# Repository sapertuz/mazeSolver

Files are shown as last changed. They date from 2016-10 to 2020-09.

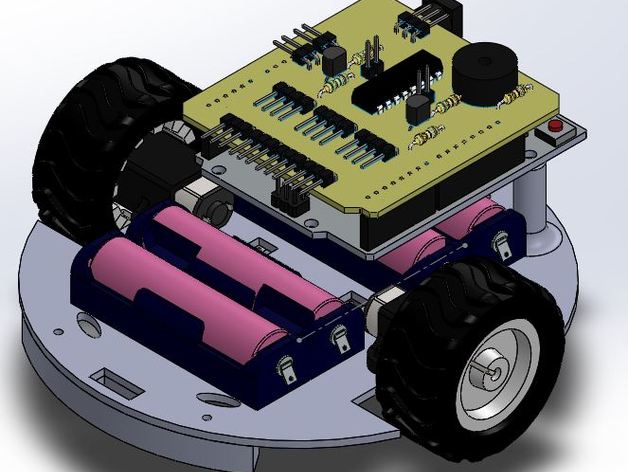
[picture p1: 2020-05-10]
Maze_Solver/images/dd3d5e054d19bdba38d1fe2deb0f85b0_preview_featured.JPG

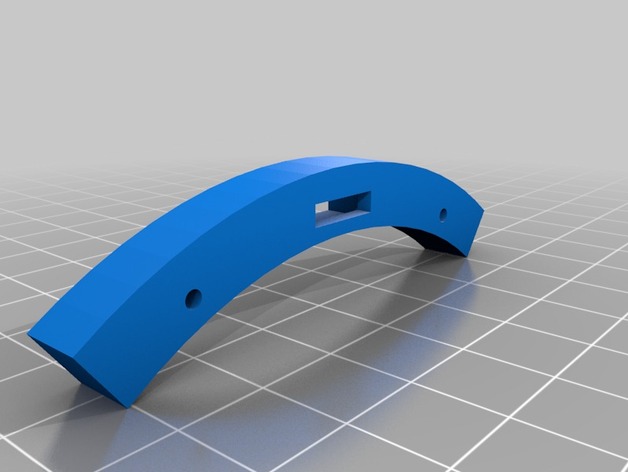
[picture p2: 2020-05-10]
Maze_Solver/images/59abfc2566f2f89f3f8ee435759e22d9_preview_featured.jpg

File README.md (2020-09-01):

<h1 align="center">Open-Source mazeSolver</h1>
<div align="center">

<i>A Maze Solving Line Follower Using Arduino</i>








Awesome Badge

<!-- <img src="http://hits.dwyl.com/cheiio/mazeSolver.svg" alt="Hits Badge"/> -->

<br>
<i>Loved the project? Please consider giving a Star ⭐️ to help it improve!</i>

</div>

# mazeSolver

<a href="https://github.com/cheiio/mazeSolver">
  Twitter
</a>

This Git contains the 
- Arduino Project Source  https://github.com/cheiio/mazeSolver/tree/master/Arduino_src
- Eagle Source for PCB board  https://github.com/cheiio/mazeSolver/tree/master/Laberinto
- SolidWorks files of parts to be printed  https://github.com/cheiio/mazeSolver/tree/master/Maze_Solver/files

This is the arduino program running ont he maze solver project viewed in http://www.thingiverse.com/thing:1690543
You need the PID_v1 library fot arduino to make irt run

This is a current working project. It's a 3D printed Maze Solver and Line Follower based on the Pololu 3Pi robot.
It uses a Arduino Leonardo and a custom made shield.
<br />

## Materials

***<details><summary>Click Me For Materials!GIF</summary>***
  
* Arduino Leonardo
* L293D
* Piezo Buzzer
* QTR-1RC Reflectance Sensor (2-Pack) x 2 (https://www.pololu.com/product/2459)
* QTR-8A Reflectance Sensor Array (Only the cutted 2 sensor at the left) https://www.pololu.com/product/960
* 75:1 Micro Metal Gearmotor HPCB 6V (https://www.pololu.com/product/3064)
* Pololu Wheel 42×19mm Pair (https://www.pololu.com/product/1090)
* Pololu Micro Metal Gearmotor Bracket Pair
* (https://www.pololu.com/product/989)
* Pololu Ball Caster with 1/2″ Metal Ball (https://www.pololu.com/product/953)
* 2-AA Batteries
* 2-AA Battery Holder (https://www.pololu.com/product/1150)
</details>
<br />

### Robot In Action

<a href="https://www.youtube.com/watch?v=Ddkci5myxYI" target="_blank">
GIF
</a>
<br />

## CAD Files

</a>
<a href="https://github.com/cheiio/mazeSolver/tree/master/Maze_Solver/files/" >
  CAD Files
</a>
</a>
<a href="https://github.com/cheiio/mazeSolver/tree/master/Maze_Solver/files/" >
  CAD Files
</a>
</a>
<a href="https://github.com/cheiio/mazeSolver/tree/master/Maze_Solver/files/" >
  CAD Files
</a>

<br /><br />

## Line Follower Photos

CAD Files
CAD Files

<br />

## YouTube Video
</a>
<a href="https://www.youtube.com/watch?v=Ddkci5myxYI&feature=youtu.be" >
  CAD Files
</a>

For Robot in action Please checkout my<br />
**Youtube Channel  [Click Here](https://www.youtube.com/watch?v=Ddkci5myxYI&feature=youtu.be)** .<br /><br /><br />

If You Found this Project Useful in any manner <br />
**Subscribe** my **Youtube Channel  [Click Here](https://www.youtube.com/user/Sapmcool)** .<br />

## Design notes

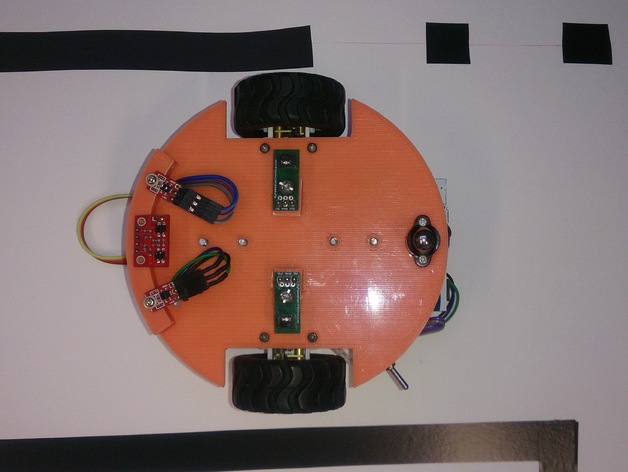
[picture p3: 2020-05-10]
Maze_Solver/images/c2a115ca9fa706efb5667b804ab19a76_preview_featured.JPG

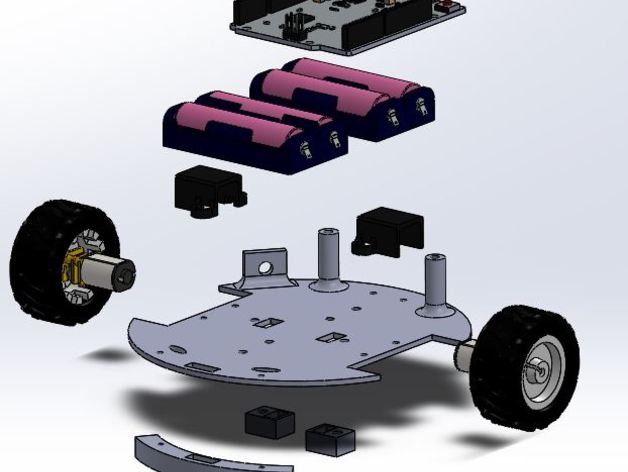
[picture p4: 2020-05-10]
Maze_Solver/images/6491ceb7f1e24ea76eec02fb2ce37934_preview_featured.JPG

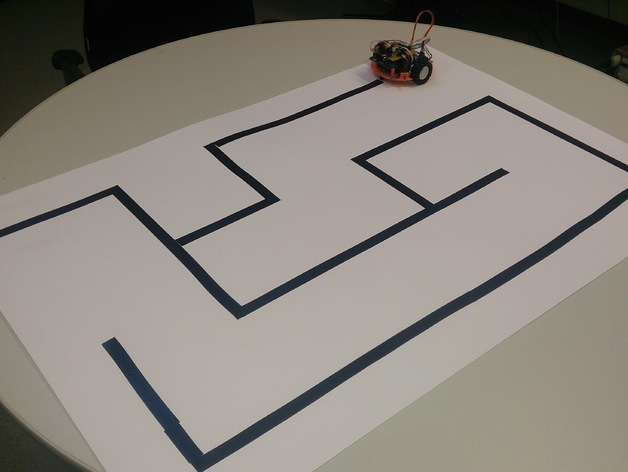
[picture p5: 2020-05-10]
Maze_Solver/images/3bacaf6ce22a14ae35e1a1dbc1d07312_preview_featured.JPG

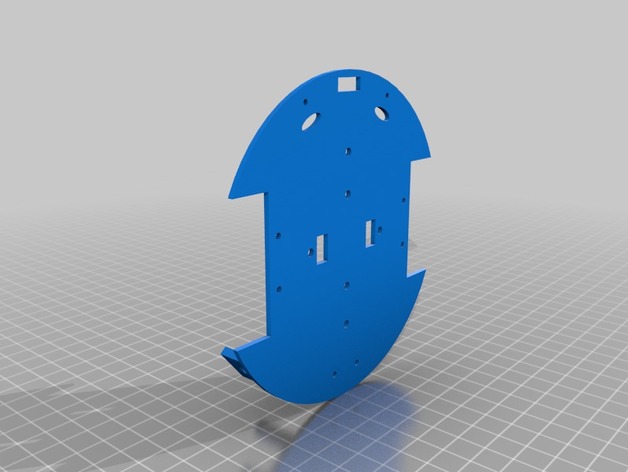
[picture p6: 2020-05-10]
Maze_Solver/images/ea35e3248423d630fb57c955e7d1f504_preview_featured.jpg

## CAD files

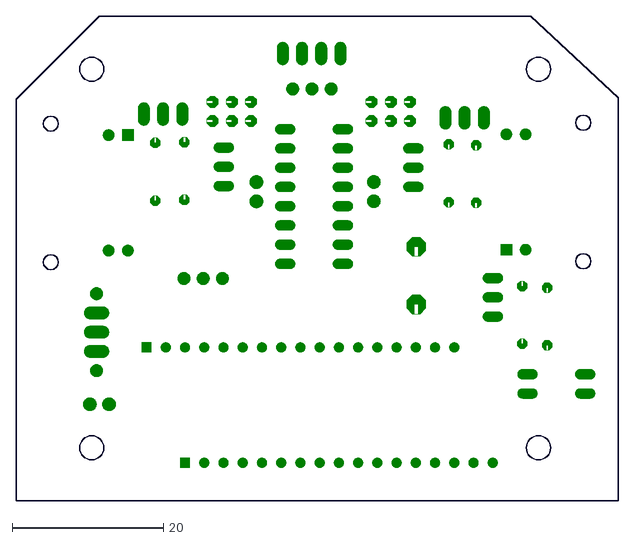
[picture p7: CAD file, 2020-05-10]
Laberinto/placa.dxf
79.5 x 64.0

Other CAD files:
Maze_Solver/files/2.STEP
Maze_Solver/files/1.STEP
Maze_Solver/files/base.STEP
Maze_Solver/files/1.SLDPRT
Maze_Solver/files/1.STL
Maze_Solver/files/2.SLDPRT
Maze_Solver/files/2.STL
Maze_Solver/files/base.SLDPRT
Maze_Solver/files/base.STL

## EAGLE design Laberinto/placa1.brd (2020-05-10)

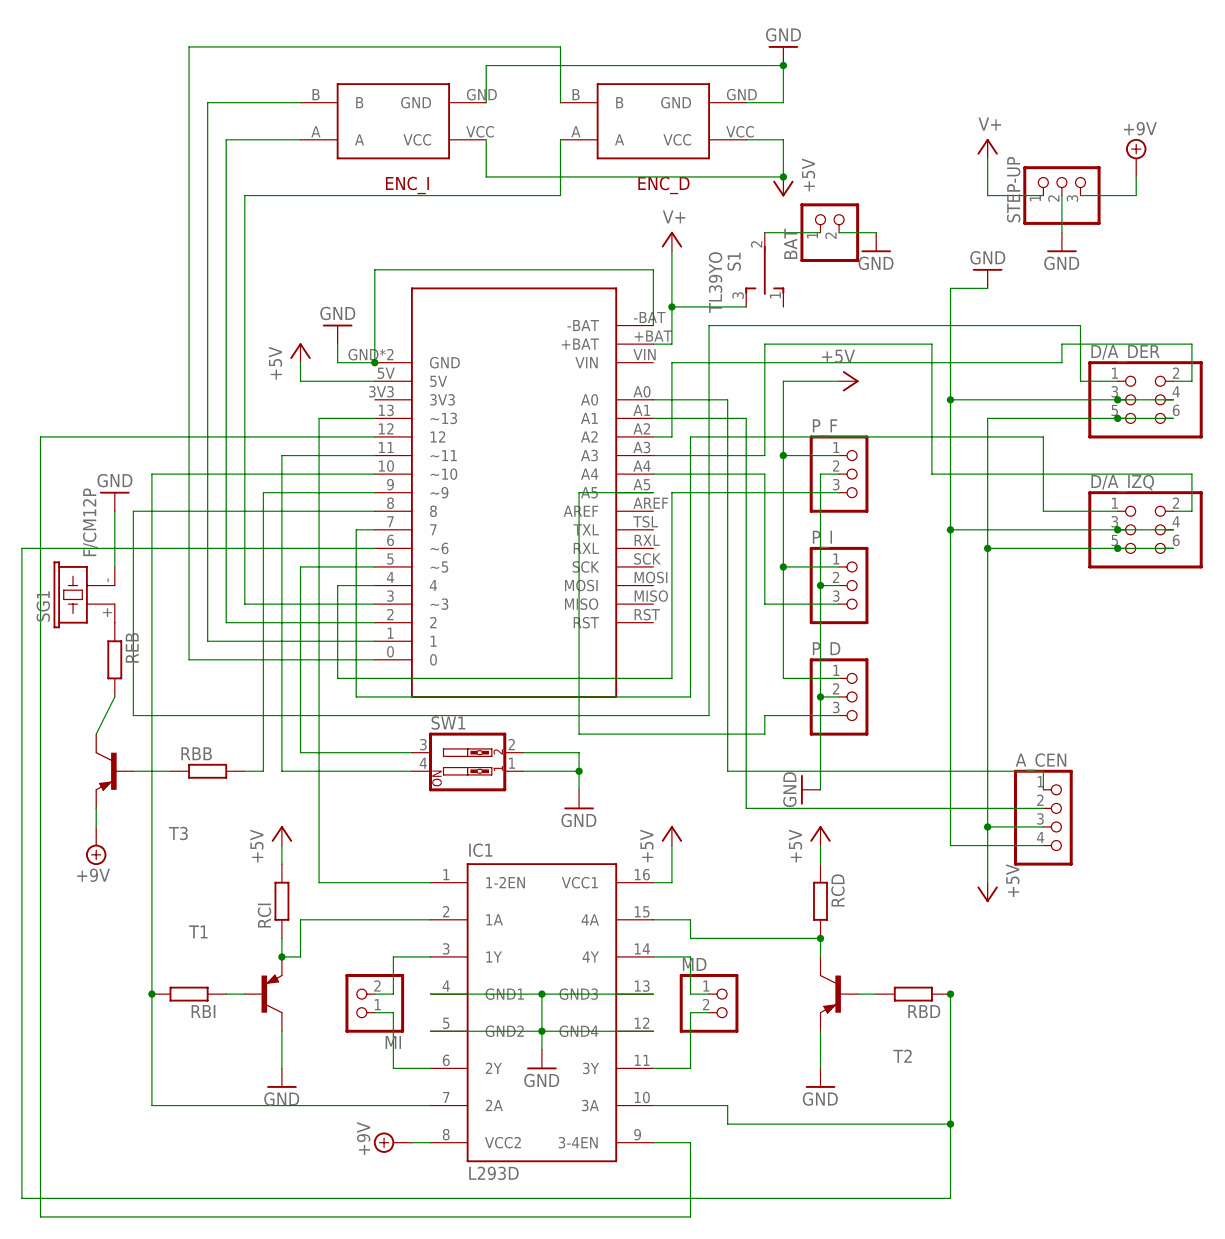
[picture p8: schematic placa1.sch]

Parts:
A_CEN: PINHD-1X4/90; 1X04/90
BAT: PINHD-1X2; 1X02
D/A_DER: PINHD-2X3/90; 2X03/90
D/A_IZQ: PINHD-2X3/90; 2X03/90
ENC_D: POLOLU_ENCODER
ENC_I: POLOLU_ENCODER
IC1: L293D; DIL16
MD: PINHD-1X2; 1X02
MI: PINHD-1X2; 1X02
P_D: PINHD-1X3/90; 1X03/90
P_F: PINHD-1X3; 1X03
P_I: PINHD-1X3/90; 1X03/90
RBB: R0204/7; 0204/7
RBD: R0204/7; 0204/7
RBI: R0204/7; 0204/7
RCD: R0204/7; 0204/7
RCI: R0204/7; 0204/7
REB: R0204/7; 0204/7
S1: TL39YO; TL3XYO
SG1: F/CM12P
STEP-UP: PINHD-1X3; 1X03
SW1: SW_DIP-2; EDG-02
T1, T2, T3: -PNP-TO92-BEC; TO92-BEC
U$1: A-STAR_LV

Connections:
+5V: A_CEN.3, D/A_DER.5, D/A_DER.6, D/A_IZQ.5, D/A_IZQ.6, ENC_D.VCC, ENC_I.VCC, IC1.16 (VCC1), P_D.1, P_F.1, P_I.1, RCD.1, RCI.2, U$1.5V
+9V: IC1.8 (VCC2), STEP-UP.3, T3.E
GND: A_CEN.4, BAT.2, D/A_DER.3, D/A_DER.4, D/A_IZQ.3, D/A_IZQ.4, ENC_D.GND, ENC_I.GND, IC1.4 (GND1), IC1.5 (GND2), IC1.12 (GND4), IC1.13 (GND3), P_D.2, P_F.2, P_I.2, SG1.- (2), STEP-UP.2, SW1.1, SW1.2, T1.C, T2.E, U$1.-BAT, U$1.GND, U$1.GND2 (GND)
unnamed: BAT.1, S1.2
unnamed: IC1.2 (1A), RCI.1, T1.E
unnamed: RBI.1, T1.B
unnamed: RBD.2, T2.B
unnamed: IC1.15 (4A), RCD.2, T2.C
unnamed: IC1.11 (3Y), MD.2
unnamed: IC1.14 (4Y), MD.1
unnamed: IC1.7 (2A), RBI.2, U$1.10 (~10)
unnamed: IC1.3 (1Y), MI.2
unnamed: IC1.6 (2Y), MI.1
unnamed: IC1.10 (3A), RBD.1, U$1.6 (~6)
unnamed: REB.2, T3.C
unnamed: REB.1, SG1.+ (1)
unnamed: RBB.1, T3.B
unnamed: ENC_I.A, U$1.2
unnamed: ENC_D.B, U$1.0
unnamed: ENC_I.B, U$1.1
unnamed: IC1.9 (3-4EN), U$1.12
unnamed: SW1.3, U$1.5 (~5)
unnamed: SW1.4, U$1.11 (~11)
unnamed: RBB.2, U$1.9 (~9)
unnamed: ENC_D.A, U$1.3 (~3)
unnamed: IC1.1 (1-2EN), U$1.13 (~13)
unnamed: P_F.3, U$1.4
unnamed: D/A_IZQ.1, U$1.7
unnamed: D/A_DER.1, U$1.8
unnamed: A_CEN.1, U$1.A0
unnamed: D/A_IZQ.2, U$1.A3
unnamed: P_I.3, U$1.A4
unnamed: P_D.3, U$1.A5
unnamed: A_CEN.2, U$1.A1
unnamed: D/A_DER.2, U$1.A2
V+: S1.3 (S), STEP-UP.1, U$1.+BAT

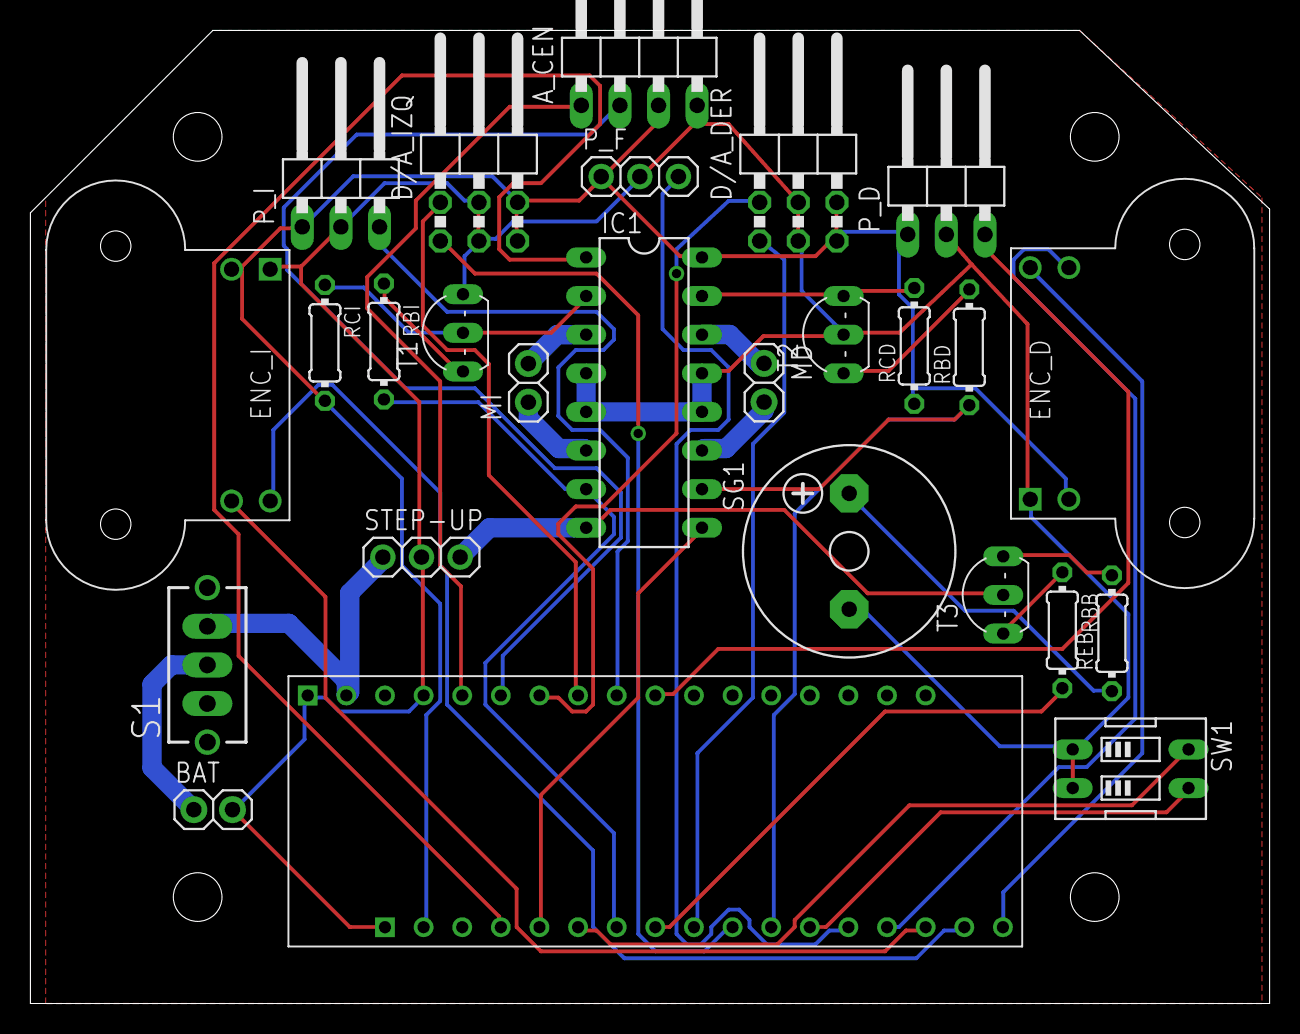
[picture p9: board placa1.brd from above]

Board: 2 copper layers, 81.5 x 64.0 mm, 26 parts (0 on the bottom side), 36 nets.

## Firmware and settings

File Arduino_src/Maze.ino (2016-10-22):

#include <PID_v1.h>

#define s3 A0
#define s1 A3
#define s2 A2
#define s0 A1
#define QRDR 7
#define QRDL 4
#define BUZZ 11
#define ENAL 5
#define ENAR 6
#define GIRL 13
#define GIRR 12

#define C  523
#define CS  524
#define D  587
#define DS  622
#define E  659
#define FA  698
#define FS  740
#define G  784
#define GS  830
#define A  880
#define AS  932
#define B  988

const unsigned int ini_notes[] = {660,660,660,510,660,770,380};
const unsigned int ini_beat[] = {100,100,100,100,100,100,100};
const unsigned int ini_mute[] ={150,300,300,100,300,550,575};

const unsigned int fin_notes[] = {G,C,E,G,C,E,C,G, GS,CS,FA,GS,CS,GS, AS,DS,G,AS,DS,G,DS, DS,DS,DS, C};
const unsigned int fin_beat[] = {100,100,100,100,100,100,100,150,100, 100,100,100,100,100,100,100,150,100, 100,100,100,100,100,100,100,150, 40,40,40, 150};

const int maxpwm = 255; // the maximum speed
const int cal=200;

int path[100], path_step = 0;

int i, x, k, ts = 50, spin = 40, halftape=100, lilbit=20, s[4];

bool flag = false;

double pos, sp=250, power_difference;
int mini0=1023, maxi0=0, mini1=1023, maxi1=0, mini2=1023, maxi2=0, mini3=1023, maxi3=0;

//Specify the links and initial tuning parameters
PID myPID(&pos, &power_difference, &sp, 10, 5, 1, DIRECT);

void setup() {
  // put your setup code here, to run once:
  pinMode(ENAR,OUTPUT);
  pinMode(ENAL,OUTPUT);
  pinMode(GIRR,OUTPUT);
  pinMode(GIRL,OUTPUT);
  pinMode(BUZZ,OUTPUT);
  pinMode(QRDL,INPUT);
  pinMode(QRDR,INPUT);

  digitalWrite(BUZZ, LOW);

  //set and turn the PID on
  myPID.SetOutputLimits(-maxpwm, maxpwm);
  myPID.SetMode(AUTOMATIC);
  myPID.SetSampleTime(50); 

  Serial.begin(9600);
  delay(2000);
  //start music
  /*for (int note = 0; note < 7; note++) {
    tone(BUZZ, ini_notes[note], ini_beat[note]);
    delay(ini_mute[note]);
  }*/

  calibrate_line_sensors();
  Serial.print(mini0);
  Serial.print("\t");
  Serial.println(maxi0);
  Serial.print(mini1);
  Serial.print("\t");
  Serial.println(maxi1);
  Serial.print(mini2);
  Serial.print("\t");
  Serial.println(maxi2);
  Serial.print(mini3);
  Serial.print("\t");
  Serial.println(maxi3);

  
  //delay(3000);
}

void loop() {

  // follow black line 
  follow_segment();
  
  if (digitalRead(QRDR)==false){ // cross section, go rigth
    read_line();
    if (!flag){
      digitalWrite(BUZZ, HIGH);
      delay(halftape);
      digitalWrite(BUZZ, LOW);
      set_motors(maxpwm,maxpwm);
      delay(halftape);
      rigth_sensor();
    }
  }
    
  if (flag){                            // white space
    
    flag = false;
    set_motors(maxpwm,maxpwm);
    bool l, r;
    for (i=1;i<lilbit;i++){             // advance a little bit or until turn l/r is found
        delay(ts);
        l = !digitalRead(QRDL);
        r = !digitalRead(QRDR);
        if (l || r){
          digitalWrite(BUZZ, HIGH);
          delay(halftape);
          digitalWrite(BUZZ, LOW);
          l = l | !digitalRead(QRDL);
          r = r | !digitalRead(QRDR);
          if ((l && r) || r){       
            rigth_sensor();             // turn rigth
          }else{
            left_sensor();              // turn left
          }
          break;
        }
    }
    
    if (i == lilbit){
      read_line();
      if (flag){
        flag = false;
        digitalWrite(BUZZ, HIGH);
        delay(halftape);
        digitalWrite(BUZZ, LOW);
        turn_around();
      }else{
        int cont = 0;
        do {
          cont++;
          follow_segment();
        }while(!flag && cont < lilbit);
        if (flag){
          flag = false;
          set_motors(-maxpwm,-maxpwm);
          set_motors(0,0);
          //FINISH music
  /*        for (int note = 0; note < 27; note++) {
            tone(BUZZ, fin_notes[note], fin_beat[note]);
          }
 */         while(1);
        }
      }
      
    }
  }
/*  read_line();
  Serial.print(s[0]);
  Serial.print(",");
  Serial.print(s[1]);
  Serial.print(",");
  Serial.print(s[2]);
  Serial.print(",");
  Serial.println(s[3]);
  //Serial.print(power_difference);
  //Serial.print('\t');
  Serial.println(pos);
  delay(100);
  */
  flag = false;
}

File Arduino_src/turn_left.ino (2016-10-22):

// function used to turn the robot rigth

void left_sensor(){
/*  set_motors(-maxpwm,-maxpwm);
  delay(10);
  set_motors(0,0);
  delay(2000);
  
  set_motors(maxpwm,maxpwm);
  delay(halftape);
  
  set_motors(-maxpwm,-maxpwm);
  delay(10);
  set_motors(0,0);
  delay(2000);
    
  set_motors(-1*maxpwm,maxpwm);
  delay(spin);

  set_motors(maxpwm,-maxpwm);
  delay(10);
  set_motors(0,0);
  delay(2000);
  
  for(k=1;k<=lilbit;k++){
    follow_segment();
  }
  
  set_motors(-maxpwm,-maxpwm);
  delay(10);
  set_motors(0,0);
  delay(2000); 
*/
  
  set_motors(-1*maxpwm,maxpwm);
  delay(spin);

  for(k=1;k<=lilbit;k++){
    follow_segment();
  }
  
}

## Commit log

2016-10-22 Maze Solver Robot
    Arduino project for the maze solver robot made by Sergio Pertuz; It
    needs the PID_v1.h library for arduino
2020-05-10 new files, complete project
    [1.SLDPRT, 1.STEP, 1.STL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]
